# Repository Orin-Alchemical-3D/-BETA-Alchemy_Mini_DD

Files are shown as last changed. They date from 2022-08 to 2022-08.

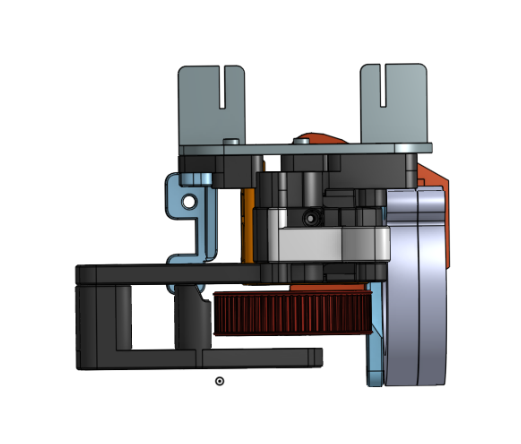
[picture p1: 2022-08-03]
BETA_2.4/BETA_2.4_IMAGES/TOP.png

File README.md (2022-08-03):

# BETA_Alchemy_Mini_Direct_Drive
Small footprint &amp; lightweight direct drive extrusion system.

# Join the community discussion, get assistance, or even show off your mods!  
# DISCORD: https://discord.gg/aE49DW2xXe

-----------------------------------------------------------------------------------------------------------------------------------------------------------

!!!!  PLEASE READ THESE NOTES PRIOR TO CONTINUING WITH YOUR BUILD !!!!

A)  I will be releasing a model cooler assembly for this hotend shortly as well, so if you do not have something that works with it right away,
please keep an eye on this repository for the design.

B)  This assembly comes in relatively close conditions to a hotend and a working stepper motor.  I will not support issues due to using materials such as PLA to build the assembly.  PLA and similar materials are NOT suitable to build 3D printer parts out of, please do not ask if PLA is ok, it is not.  If you are going to use PETG for the build, please keep an eye on the motor mount area and consider reducing current to your motor.  Steppers produce heat and PETG (while better than PLA) still has a lower TG point, it could warp.

C)  THIS IS A BETA RELEASE AND NOT THE FINAL PRODUCT, YOU ARE RESPONSIBLE FOR YOUR SAFETY AND EQUIPMENT WHEN BUILDING AND USING THIS SYSTEM AND 
YOU ACCEPT ALL LIABILITY BY USING THESE FILES FROM THIS BETA TO RELEASE CANDIDATES AND POST!

-----------------------------------------------------------------------------------------------------------------------------------------------------------

# PREFACE

This is the first rendition of the Alchemy_Mini_DD.   This system's initial design is based on the Voron Jetpack motion components.  

Creation of this system was inspired by the lack of existing direct drive solutions on the market and in maker space which compare with the likes 
of the E3D Hemera and BIQU H2, etc.  Units that we as individuals, can create and assemble, from available or owned materials.  Most solutions available 
to makers are gaudy, over sized, and overweight.  These negative traits have undesirable side effects when printing creating quality and speed concerns.

Much has changed in this system from its inspirational original product at the Voron project, simply put... everything changed and it really is not the same unit.   However I would like to extend a special thanks to the Voron group for their inspiration on this product and initial designs that made all of this possible so you and I can enjoy such things.  Please take a moment if you are not familiar with the Voron project to educate yourself on the hard work they commit to the makerspace.  https://vorondesign.com/

This product's initial design is centered around using with one of the most popular printers available today, the Creality Ender.   Its designed to work with the stock bolting pattern of the system.  In the very near future, additional models of this will be released to facilitate mounting on other popular systems available today, as well as variations of the system to provide more hotend compatibility.   Upcoming target printers include Prusa, Artillery, Tevo, etc.   As the product evolves so will each variation.

Upcoming models of this will include a Bowden version and a Micro version each serving their purpose with a unique twist.  The bowden is going to have some tricks up its sleeve you will not have ever seen to further improve print quality, while the micro version is going to take lightweight toolhead to the extreme.  Keep an eye out for these models as soon as this initial product leaves beta.

Once this product leaves beta, along with the additional variations, scheduled is an entire 3D print based on the principles these units bring.

-----------------------------------------------------------------------------------------------------------------------------------------------------------

# PRINT SETTINGS

Materials - ABS/ASA (Note: The parts are designed accounting for shrinkage of ASA & ABS, other filament types may or may not work.)

Layer Height - 0.20

Extrusion Width - Forced 0.4m

Infil Percentage - 40%+

Infil Type - Grid, Honeycomb, Triangle, or Cubic

Top/Bottom Wall Count - 4

Perimeter Count - 4

-----------------------------------------------------------------------------------------------------------------------------------------------------------

# B.O.M.  
Note: I am working with suppliers to distribute individual qty purchases, this early in project though some of these are multipacks, as of now Alchemical Printers is partially affiliated with both KB-3D & GulfCoast Robotics.   Both are high quality part providers with excellent customer service.

Note: This is the bare minimum, it is wise to have spare screws/heatsets etc.)

1. QTY - 15 - [M3x5x4 Heatsets](https://kb-3d.com/store/inserts-fasteners-adhesives/278-brass-heat-set-threaded-insert-for-plastic-m3x5x4mm.html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) (Be sure to get angled exterior texture, not straight)
2. QTY - 3 - [MR115-2RS Bearing](https://www.amazon.com/Miniature-Bearings-MR115-2RS-Double-Shielded-5x11x4mm/dp/B08PFT72RQ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) 
3. QTY - 2 - [GT2 16T 5mm Shaft Pully](https://kb-3d.com/store/motion/214-gates-powergrip-2gt-pulley-16-tooth-5mm-6mm-1634481998632.html?affp=6182) (Note: One of these gets the top ring pulled off, be sure your pully top is not molded and not the longer version)
4. QTY - 1 - [5x45 Shaft w/flat](https://kb-3d.com/store/hardware/141-60-5mm-bearing-steel-shafts-various-lengths-1642282491009.html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) (You can either find one with flats already, or add them yourself using a dremmel or other tool.)
5. QTY - 4 - [M3x6 Set Screw](https://kb-3d.com/store/inserts-fasteners-adhesives/624-alloy-set-screw-m3-x-05-x-6mm-cup-point-1656776837999.html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) (Note: This is basically a longer grub screw, FHCS might clear the support)
6. QTY - 2 - M3x8 SHCS (Socket Head Cap Screw)
7. QTY - 7 - M3x20 SHCS (Socket Head Cap Screw)
8. QTY - 2 - M3x25 SHCS (Socket Head Cap Screw)
9. QTY - 1 - [BondTech BMG Extruder Internals Kit](https://kb-3d.com/store/bondtech/484-bondtech-bmg-extruder-internals-kit-build-your-own-1645151327973.html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) (Some clones have the correct components for this build internally)
10. QTY - 1 - [GT2 158MM Closed Loop Belt](https://www.amazon.com/2GT-Timing-Belt-Closed-Loop/dp/B014QKEH26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) 
11. QTY - 1 - [Nema17 42x42x20 16Ncm](https://kb-3d.com/store/stepper-motors/66-ldo-slim-power-extruder-stepper-pancake-motor-42sth25-1404mac-1644693835267.html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) (You cannot use steppers with longer bodies without modifying the system, thus noted here.)
12. QTY - 1 - [E3D V6 or Clone](https://gulfcoast-robotics.com/collections/hotends/products/all-metal-v6-hotend-black-edition) or [E3D Revo-Six](https://kb-3d.com/store/extruders-hotends/425-e3d-rapid-change-revo-hotend-six-24v-1640229946834.html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) or any other hotend using the V6 style clamp mounting system.

Highly Recommended Items Below

13. QTY - 1 - Threadlocker (Loctite Blue or similar strength, its important to note that threadlockers WILL damage ASA/ABS if they come in contact, take care when applying thread lockers that it only gets on the metal assembly.)

-----------------------------------------------------------------------------------------------------------------------------------------------------------

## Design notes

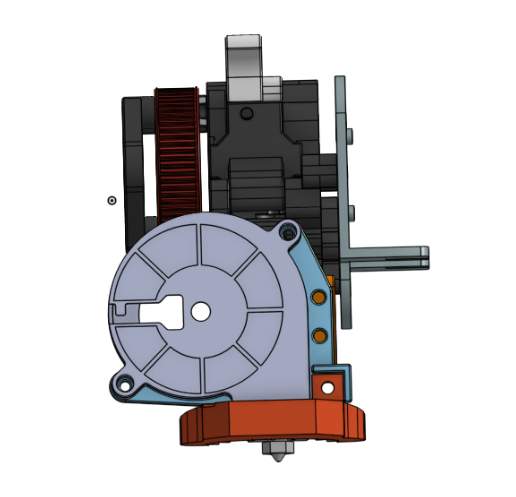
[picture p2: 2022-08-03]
BETA_2.4/BETA_2.4_IMAGES/RIGHT.png

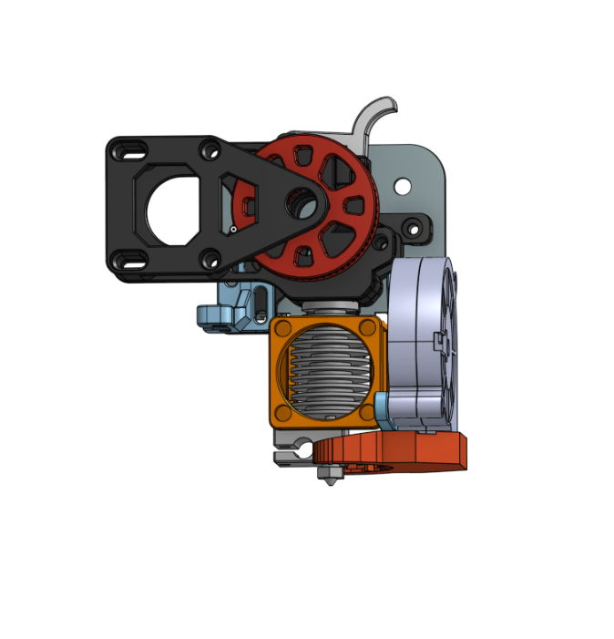
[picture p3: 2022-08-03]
BETA_2.4/BETA_2.4_IMAGES/FRONT.png

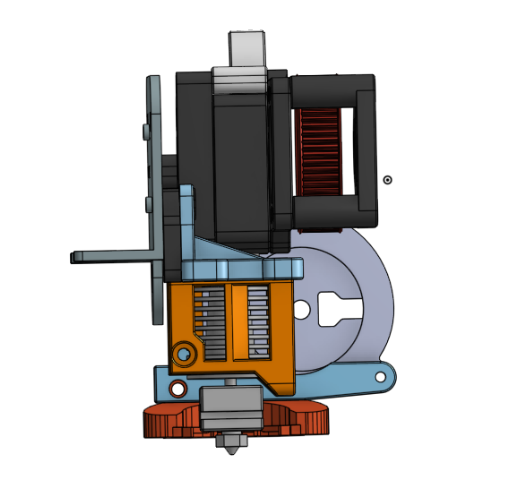
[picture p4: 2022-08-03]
BETA_2.4/BETA_2.4_IMAGES/LEFT.png

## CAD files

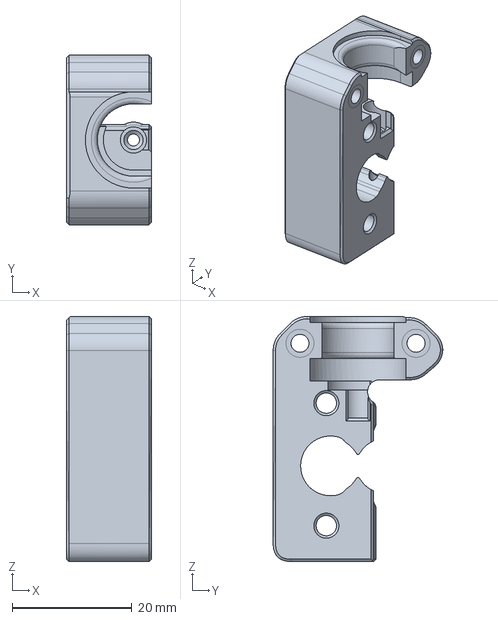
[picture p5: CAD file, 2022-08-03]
BETA_2.4/BETA_2.4_CAD/Main Body.step
14.2 x 28.4 x 41.0 mm

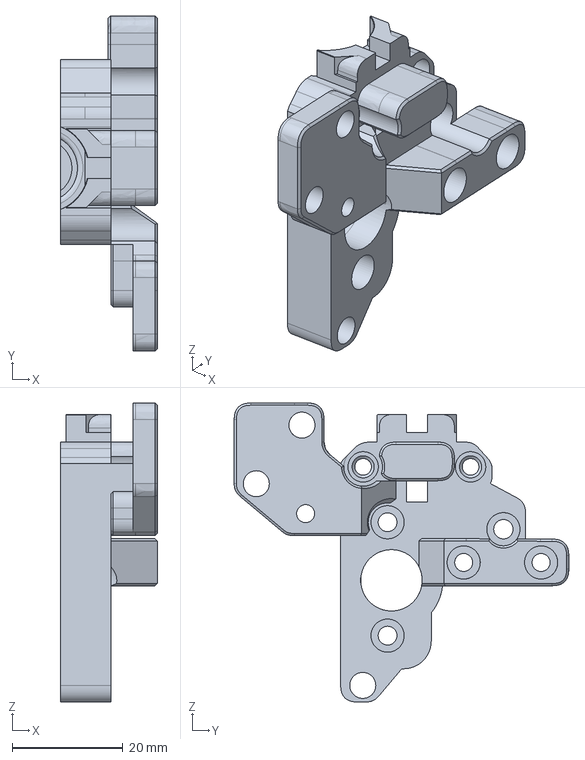
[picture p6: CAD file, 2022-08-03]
BETA_2.4/BETA_2.4_CAD/BETA_v2.3_Front_Plate.step
17.5 x 60.5 x 54.1 mm

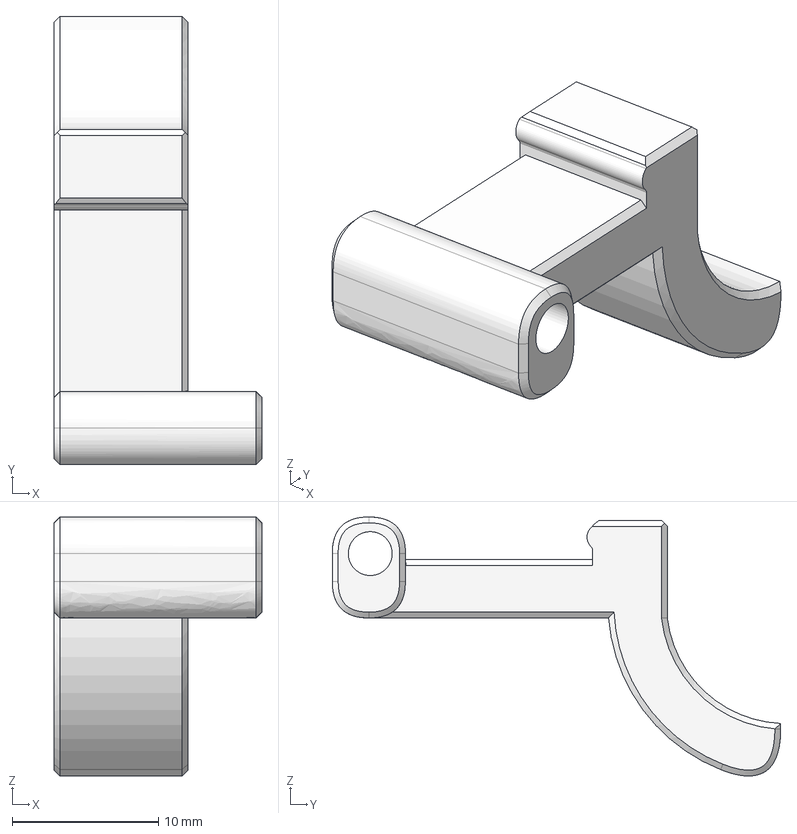
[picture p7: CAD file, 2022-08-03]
BETA_2.4/BETA_2.4_CAD/Locking_Arm.step
14.2 x 30.6 x 17.7 mm

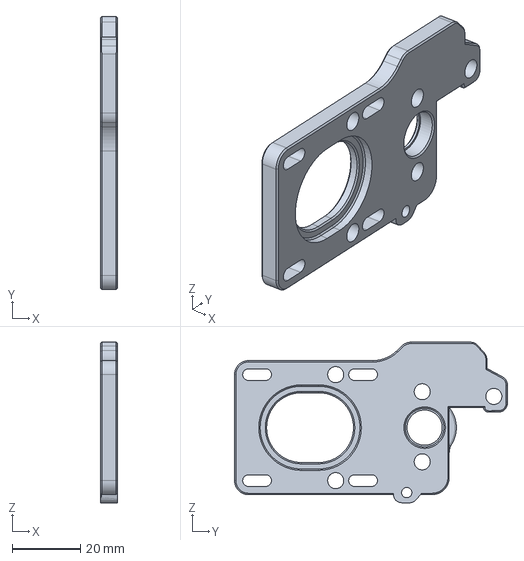
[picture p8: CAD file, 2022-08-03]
BETA_2.4/BETA_2.4_CAD/Motor Plate.step
5.00 x 79.8 x 47.0 mm

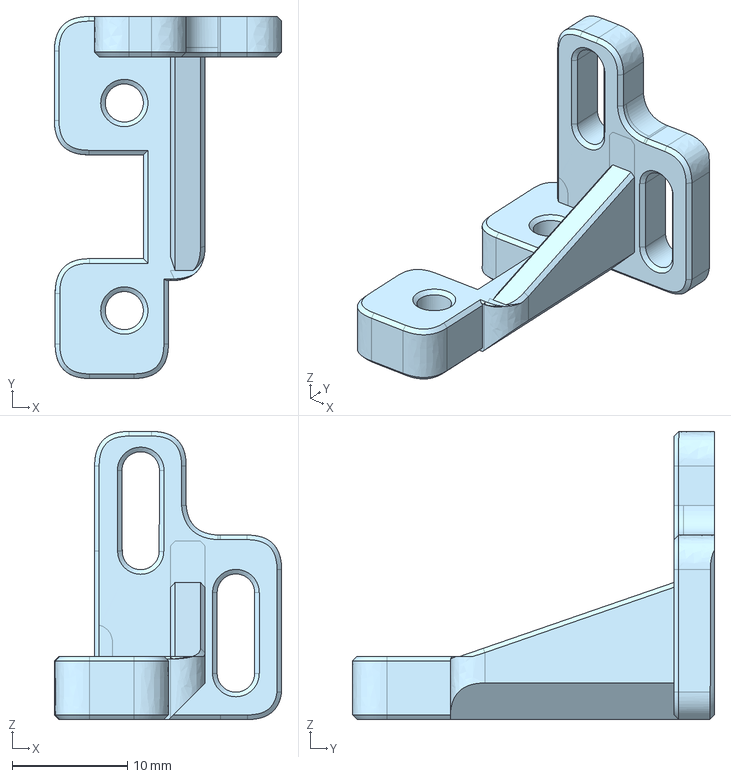
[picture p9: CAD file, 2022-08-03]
BETA_2.4/BETA_2.4_CAD/CRTouch_Bracket.step
19.7 x 31.4 x 25.0 mm

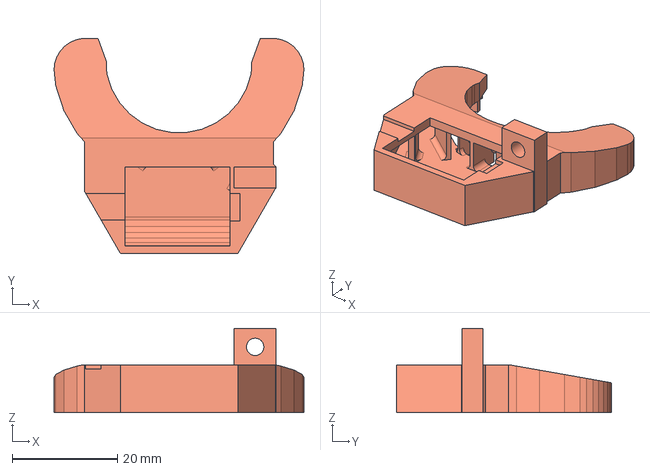
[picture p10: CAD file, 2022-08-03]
BETA_2.4/BETA_2.4_CAD/prusa nozzle fan (1).step
47.6 x 41.0 x 16.0 mm

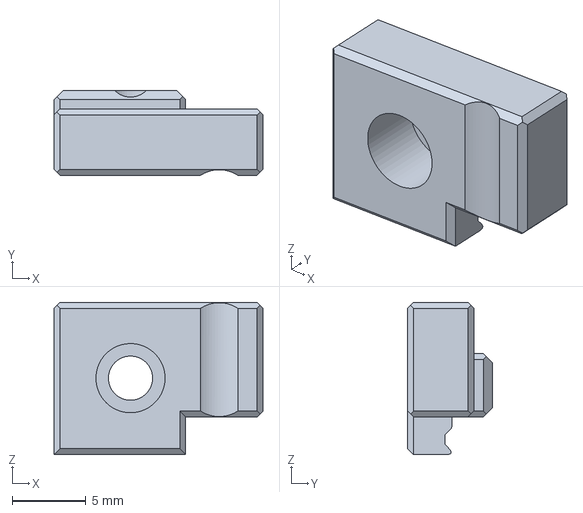
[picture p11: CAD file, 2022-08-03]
BETA_2.4/BETA_2.4_CAD/Tension_Block.step
14.2 x 5.75 x 10.3 mm

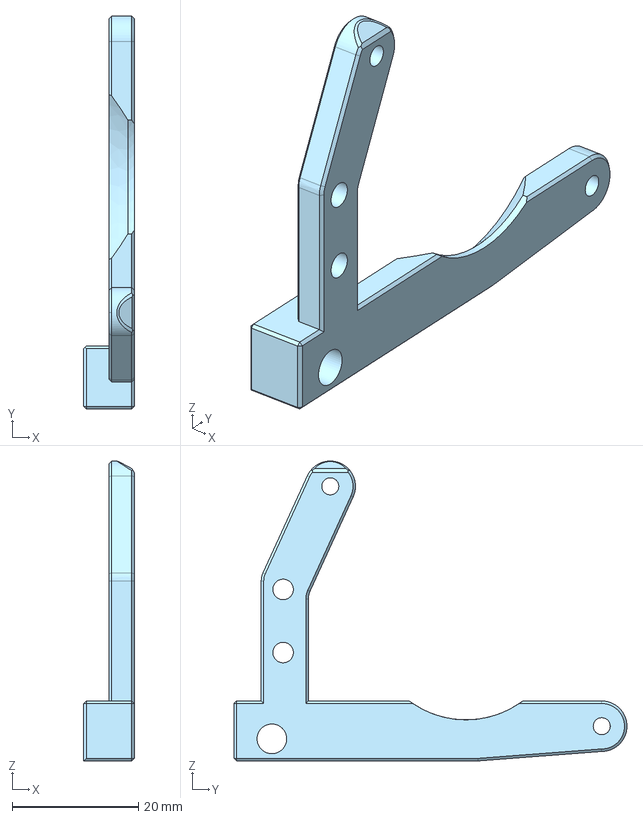
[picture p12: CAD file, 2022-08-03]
BETA_2.4/BETA_2.4_CAD/5015_Fan_Adaptor.step
8.00 x 62.2 x 47.5 mm

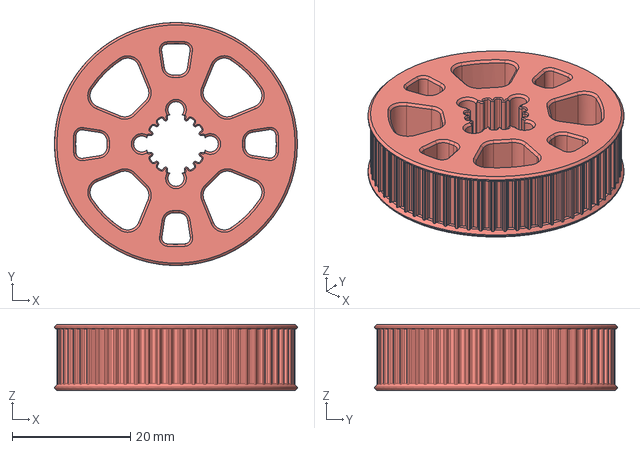
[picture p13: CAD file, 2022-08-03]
BETA_2.4/BETA_2.4_CAD/64T Front Pulley Gear (VORON).step
41.0 x 41.0 x 11.2 mm

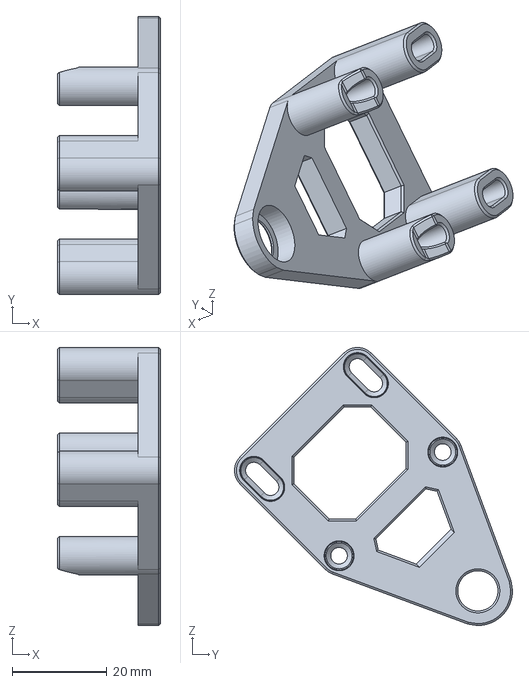
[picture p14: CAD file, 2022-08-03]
BETA_2.4/BETA_2.4_CAD/Rear Brace.step
21.8 x 58.8 x 58.8 mm

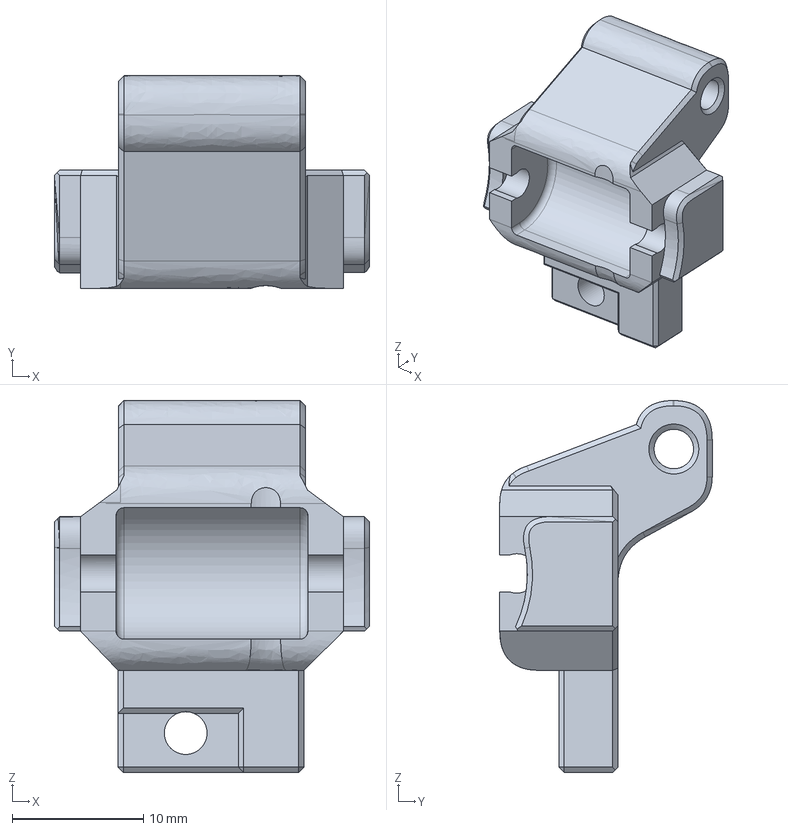
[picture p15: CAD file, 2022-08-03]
BETA_2.4/BETA_2.4_CAD/Guider.step
24.0 x 16.2 x 28.3 mm

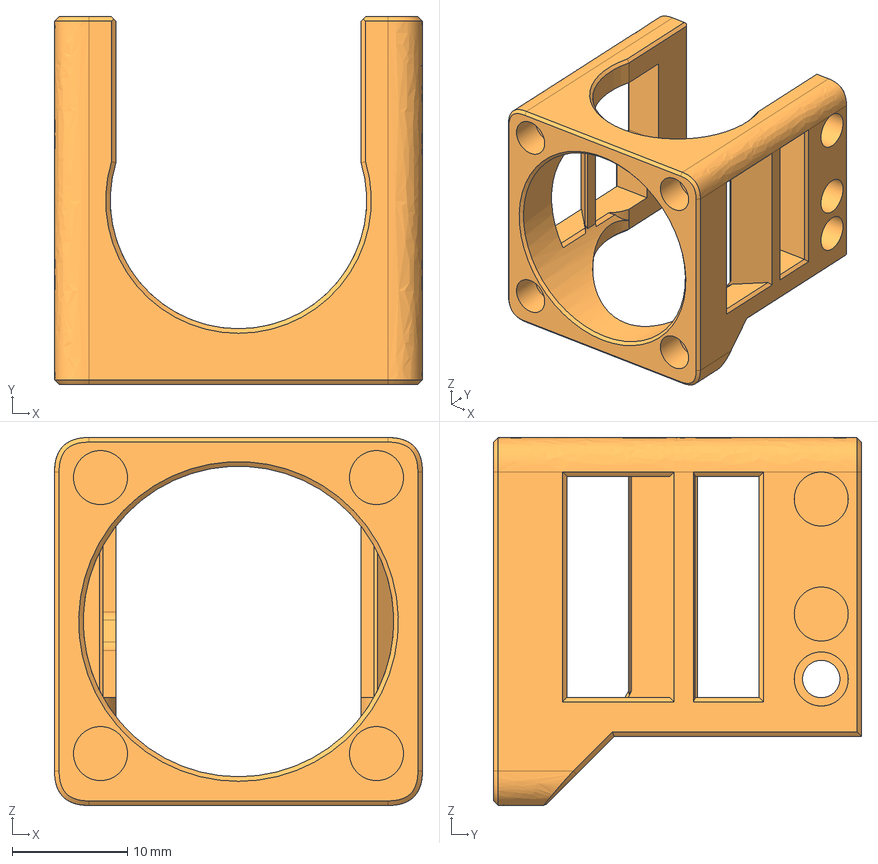
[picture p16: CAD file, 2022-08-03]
BETA_2.4/BETA_2.4_CAD/3010_V6_Shroud.step
32.0 x 32.0 x 32.0 mm

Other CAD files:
BETA_2.4/BETA_2.4_STL/3010_V6_Shroud.stl
BETA_2.4/BETA_2.4_STL/5015_Fan_Adaptor.stl
BETA_2.4/BETA_2.4_STL/64T Front Pulley Gear (VORON).stl
BETA_2.4/BETA_2.4_STL/BETA_v2.3_Front_Plate.stl
BETA_2.4/BETA_2.4_STL/CRTouch_Bracket.stl
BETA_2.4/BETA_2.4_STL/Guider.stl
BETA_2.4/BETA_2.4_STL/Locking_Arm.stl
BETA_2.4/BETA_2.4_STL/Main Body.stl
BETA_2.4/BETA_2.4_STL/Motor Plate.stl
BETA_2.4/BETA_2.4_STL/Rear Brace.stl
BETA_2.4/BETA_2.4_STL/Tension_Block.stl
BETA_2.4/BETA_2.4_STL/prusa nozzle fan (1).stl

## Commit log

2022-07-17 BETA_Release
    This is the first rendition of this hardware. Uploading to GitHub to distribute to initial testers for equipment.
    [BETA_64T_Front_Pulley_Gear.stl, BETA_CRTouch_Bracket_V2.stl, BETA_Front_Plate.stl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]
2022-07-19 BETA V.2
    Updating beta files to include revision 2 of the Alchemy_Mini_DD
    [BETA_v2_64T_Front_Pulley_Gear.step, BETA_v2_Front_Plate.step, BETA_v2_Guide.step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]
2022-07-19 BETA V2.0 Update
    Uploading BETA 2.0 of Alchemy_Mini_DD
    [64T Front Pulley Gear (1).stl, Front Plate (1).stl, Guider_Lock_1(1).stl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]
2022-07-19 BETA V2
    [BETA_v2_Main_Body.stl]
2022-07-20 Update README.md
    Added notes for print settings.
2022-07-21 BETA V2.1
    Some small cosmetic changes, relocation of the tension screw to be more in line with the lever, and adjustments to the frame for a shorter action on the tension arm.
    [BETA_v2.1_64T_Front_Pulley_Gear.step, BETA_v2.1_64T_Front_Pulley_Gear.stl, BETA_v2.1_Front_Plate.step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]
2022-07-22 BETA_RELEASE_2.2
    Slight rework to the locking mechanism to straighten up the recent height adjustments.
    Locking mechanism will received a more "robust" lock groove.
    The guider arm has been leveled in the locked position.
    NOTE: Cosmetic redesign of wheel has been postponed to push these changes out faster and will come on a later release.
    [64T Front Pulley Gear (1).step, 64T Front Pulley Gear (1).stl, BETA_v2.1_Front_Plate.step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]
2022-07-28 Renaming of files
    [64T Front Pulley Gear (1).stl, BETA_v2.3_Front_Plate.stl, BETA_v2.3_Guide.stl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]
